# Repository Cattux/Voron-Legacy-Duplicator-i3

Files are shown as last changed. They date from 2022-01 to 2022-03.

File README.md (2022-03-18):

# VORON Legacy Duplicator i3

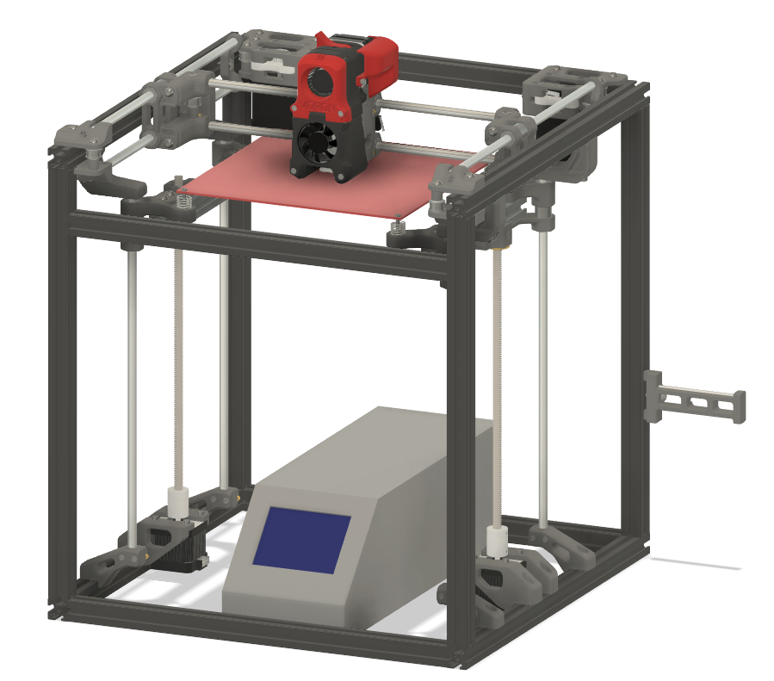
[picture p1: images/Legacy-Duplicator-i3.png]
Mock-up Design of Voron Legacy Duplicator i3


This project is still a work in progress. The printer has been physically assembled but is still getting some config tweaks and tuning done. Please use any information found here at your own discretion.

The plan for this project is to upcycle my Monoprice Maker Select 3D into a Voron Legacy, but should work for any Wanhao Duplicator i3 clones. The "plus" models will have additonal work for electronics but is out of scope since I do not have that model. Below are the goals this project was working towards or the "mission statement":

- [X] Reuse the bed from the i3
    - Requires 2 modified 3D printed parts (Qty 2 of each)
        - Z Bearing Retainer A Upper
        - Z Bearing Retainer B Upper
- [X] Forward compatible with future Legacy updates from Voron
    - don't fork this into a new printer entirely, at it's core it should still be a Voron Legacy
- [X] Require minimal rewiring
    - the wire loop was removed to split the cables to to go different places
    - The cable chain was cut off and replaced with 1/2" split wire loom tubing
    - The thermister and heater cartridge were replaced with ones that fit a E3D v6 hotend that fits in the afterburner toolhead.

# BOM 

## Configurator

Use the Configurator on the Legacy webpage to generate a full BOM. Modifications to this BOM are outlined in the next section.

1. Go to the [Legacy webpage](https://vorondesign.com/voron_legacy)
2. Click on "Configurator"
3. Choose "New Build. Give me the full BOM."
4. Choose "Blind Joints"
5. Choose "Custom Size"
6. Enter Frame Dimensions as follows:
    - Width: 410
    - Depth: 410
    - Height: 440
7. Click "Download" and save csv BOM
8. Click "Show" to see full BOM in browser

## BOM Alterations for i3 Compatibility

| Category | Part Description | Qty | Notes |
| --- | --- | --- |--- |
| Motion | <strike>TR8x8 Leadscrew Nut</strike> | <strike>2</strike> 0 | |
| Motion | Linear Shaft 8x350mm Shaft | 4 | |
| Motion | Linear Shaft 8x320mm Shaft | <strike>6</strike> 2 | |
| Motion | LM8LUU Linear Bearing | 10* | |
| Motion | GT2 Open Belt LL-2GT-6 (6mm wide) - 1690mm | 2 | |
| Motion | <strike>GT2 20T Pulley (5mm bore)</strike> | <strike>2</strike> 0 | |
| Motion | F695 Bearing | 24 | |
| Frame | <strike>2020 T-Slot Extusion - 440mm</strike> | <strike>4</strike> 0** | Replaced with next line |
| Frame | 2020 T-Slot Extusion - 410mm | 4** | |
| Frame | 2020 T-Slot Extusion - 370mm | <strike>8</strike> 4** | Qty 4 Replaced with next line |
| Frame | 2020 T-Slot Extusion - 400mm | 4** | |
| Frame | <strike>2020 T-Slot Extusion - 130mm</strike> | <strike>2</strike> 0 | Replaced with next line |
| Frame | 2020 T-Slot Extusion - 190mm | 2 | |
| Frame | 2020 Corner Brackets (MiSUMi HBLFSNB5) | 16*** | |
| Fasteners | M5x40 SHCS | 6 | |
| Fasteners | M5x30 BHCS | 12 | |
| Fasteners | M5x16 BHCS | 41 <strike>89</strike>**** | |
| Fasteners | M5x10 BHCS | 26 | |
| Fasteners | M5 Washer | 24 | |
| Fasteners | M5 T-Nut | 51 <strike>99</strike>**** | |
| Fasteners | M5 Hexnut | 4 | |
| Fasteners | M4x8 BHCS | 5 | |
| Fasteners | M3x8 SHCS | 20 | |
| Fasteners | M3x40 SHCS | 5 | |
| Fasteners | M3x30 SHCS | 20 | |
| Fasteners | M3x20 SHCS | 8 | |
| Fasteners | M3x16 SHCS | 16 | |
| Fasteners | M3x12 SHCS | 8 | |
| Fasteners | M3 Threaded Insert | 43 | |
| Fasteners | M2x10 Self-Tapping Screw | 8 | |
| Fasteners | <strike>Bed Spring 1" L 0.408" OD</strike> | <strike>4</strike> 0 | | 
| Electronics | <strike>E3D V6 Bowden Hotend Kit (24V)</strike> | <strike>1</strike> 0 | Replaced with next line | 
| Electronics | E3D V6 Bowden Hotend Kit (12V) | 1 | | 
| Electronics | <strike>PL-08N Inductive Probe</strike> | <strike>1*****</strike> | Replaced with next line |
| Electronics | BLTouch | 1***** | |
| Clockwork | BMG dual drive extruder kit | 1 | | 

&ast;Possible to reuse 2 linear bearings from i3, if they can be removed from the bearing block.

&ast;&ast;Not strictly required, but I think the assembly is easier with these modified lengths.

&ast;&ast;&ast;These aren't on the original BOM, the design intent is to have the ends of the extrusions tapped and drilled so that they can be screwed together with M5 bolts. In fact the design doesn't allow for them in all corners. I used them anyway since I already bought them, but I'd suggest leaving them off.

&ast;&ast;&ast;&ast; I originally added more to the BOM for the corner brackets, but the corner brackets are totally not required. 

&ast;&ast;&ast;&ast;&ast;I am going to keep using my BLTouch as I really like printing on glass and the inductive probes only work on a spring steel plate.

Other than the above categories, the rest of the BOM categories should be safe to ignore. I included a few lines from the "Electronics" category because they're required for the Afterburner extruder module. I also added a line for the BMG dual drive extruder kit because I plan on keeping this a direct drive printer, not a bowden printer like the default Legacy build has.

## Printed Parts

With 5 exceptions, all printed parts can be sourced from [Voron directly](https://github.com/VoronDesign/Voron-Legacy/releases/tag/V1.0). This repo was forked from the original Voron Legacy repo at release v1.0 and all STLs are still present in this repo for completeness, but it is best practice to get the latest files directly from Voron.

- The Z Bearing Retainer A Upper and Z Bearing Retainer B Upper needed to be modified to move the bed mounting hole 3mm away from the bearing hole in the X direction.
- The install location of the "Z Shaft Support - Lower" also needs to be moved which required a redesign of the "Z Alignment Jig".
- The x_carriage_left and x_carriage_right were modified to house a BLTouch instead of the induction probe. This is not required, but it's a not neater to have it hidden inside the carriage rather than hanging off the side. This way it's as close to the nozzle as possible as well. 

These modified STLs are available in the STLs/i3 folder of this repo **with the exception being the BLTouch carriage. The carriage files are not yet in this repo as my original design worked but wasn't super robust; it's easy to accidentally bump the BLTouch out of place.**

# CAD

The Voron Legacy Fusion 360 model was used to generate the modified STLs. This modified model is available along with the original in the CAD folder of this repo as well as a .STEP export or each.

# Firmware

The firmware of choice for Vorons is Klipper, which works on the stock Melzi board as well as pretty much anything else that can run an FDM printer. My i3 has an SKR-Mini E3 v2.0, so when I get that far there will be a "skr-mini_e3_v2.0_config.cfg" file in the Firmware folder of this repo. 

Please note that I've left the default "skr_v1.3_config.cfg" file in this repo for now as reference, but it has not been reconfigured for the "Legacy Reduplicator i3" print volume or internals.

# VORON Legacy Source Info

Image of Voron Legacy

This repo was forked on Jan 18, 2022 and may be out of date from the original. Please see the official release of the Voron Legacy 3d printer at the [Voron Design]( http://vorondesign.com/voron_legacy) website.

Voron Logo

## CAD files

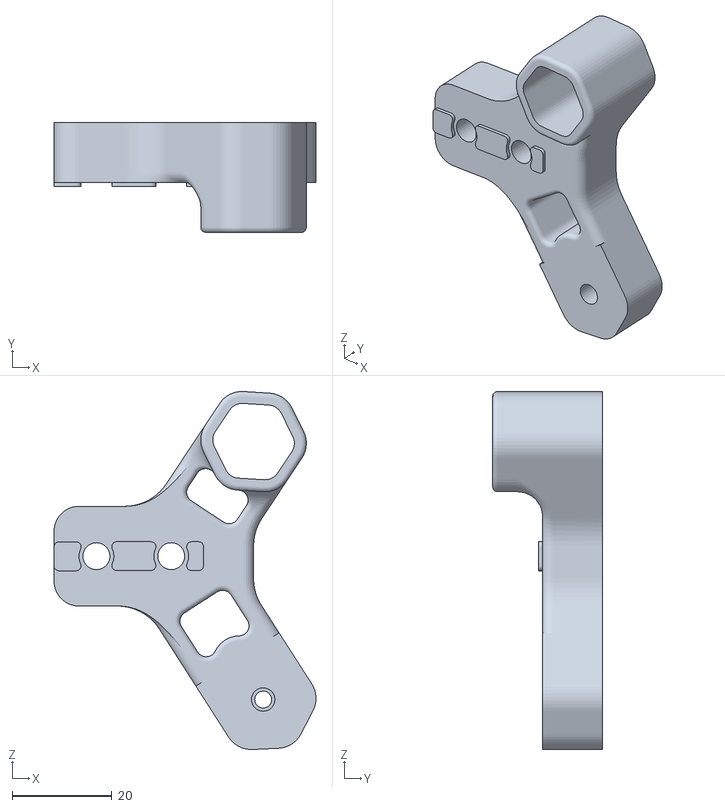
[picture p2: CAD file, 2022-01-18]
STLs/i3/Z Bearing Retainer A - Upper i3.stl
52.5 x 22.0 x 71.8

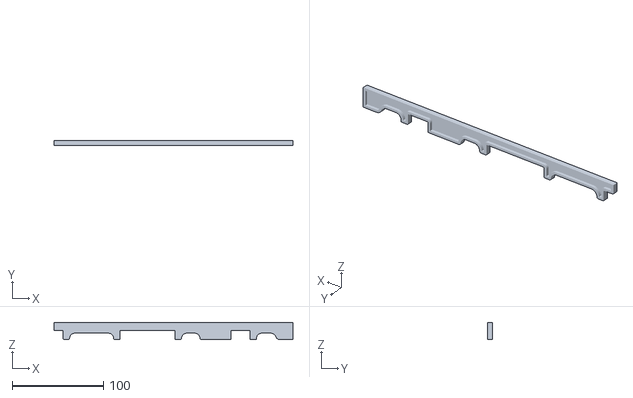
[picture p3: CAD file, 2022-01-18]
STLs/i3/Z Alignment Jig i3.stl
262.3 x 5.00 x 18.8

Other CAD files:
STLs/i3/Z Bearing Retainer B - Upper i3.stl

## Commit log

2022-01-18 initial commit of Legacy Duplicator i3
    [Z Alignment Jig i3.stl, Z Bearing Retainer A - Upper i3.stl, Z Bearing Retainer B - Upper i3.stl]
2022-01-20 Added extruder parts to BOM
